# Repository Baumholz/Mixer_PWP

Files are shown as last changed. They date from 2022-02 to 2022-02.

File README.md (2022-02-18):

# PWPHardwareMonkeys

This project consists of two WoT devices. The files for the esp32 can be found in the mixer / dispenser folders.

##  Dispenser

### Requirements

To use the dispenser you need:

- ESP32 (flashed with micropython -> main logic)
- ESP01s (flashed with arduino -> handles button and servo motor logic)
- Switchbot
- Rotary Switch
- Keyboard Switch (Kailh box jade or similar)
- Light Sensor (tsl2591 or similar)
- Cables
- Either Screws, Glue or a Soldering iron to assemble the dispenser
- 3d Printed Parts [STL Files](dispenser/dispenser_stls)

Optionally:
- Ws2812b LED Strip
- Usb-C breakout board for esp01 for easier power delivery

### Structure
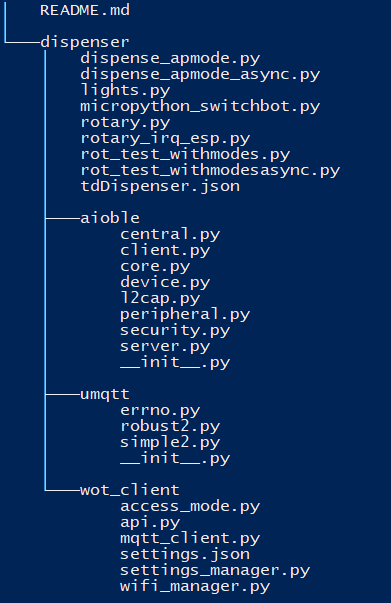
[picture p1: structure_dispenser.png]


### Components / Interfaces
The dispenser has 3 main features

1. [MQTT interface](dispenser/wot_client/api.py) maintained by the modes & communication group 
2. [Switchbot interface](dispenser/micropython_switchbot.py) which can be accessed via API or Bluetooth
3. [Rotary encoder](dispenser/rotary_irq_esp.py) for switching the four security states

### Setup

1. Print and assemble dispenser 
2. Flash esp32 with micropython and wire components to the esp32 (GND and 3.3V/5V can be daisy chained between components)
    1. Connect rotary encoder (clk/s1 = gpio27, dt/s2 = gpio26)
    2. Connect Light sensor to scl and sda (predefined as 5 and 4, but can be changed inside of the tsl2591 python module in line 55)
    3. Optionally: Connect LED Strip to gpio25
3. Copy files on root directory of the esp
4. Configure Wifi credentials in [settings.json](dispenser/wot_client/settings.json)
5. Configure Switchbot bluetooth mac address in [micropython_switchbot.py](dispenser/micropython_switchbot.py) in line 39
6. Run [main.py](dispenser/main.py) on esp
7. Follow instructions of the selected security mode
8. Copy arduino code onto the esp01s and wire components 
    1. connect keyboard switch to gpio2
    2. connect servo motor to gpio0

## Mixer

### Requirements

To use the mixer you need:

- ESP32 (flashed with micropython)
- LEDs
- Rotary Switch
- Mixer
- Cables
- Resistors

### Structure
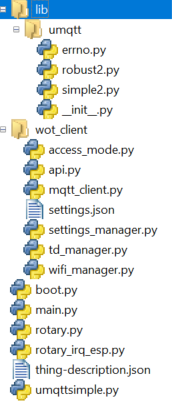
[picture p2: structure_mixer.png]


### Components / Interfaces
The Mixer has 2 main features

1. [MQTT interface](mixer/wot_client/api.py) maintained by the modes & communication group 
2. [Rotary encoder](mixer/rotary_irq_esp.py) for switching the four security states
2. [Mixer interface](mixer/main.py) which can be accessed via API

### Setup

1. Flash esp with micropython
2. Copy files on root directory of the esp
3. Configure Wifi credentials in [settings.json](mixer/wot_client/settings.json)
4. Run [main.py](mixer/main.py) on esp
5. Follow instructions of the selected security mode

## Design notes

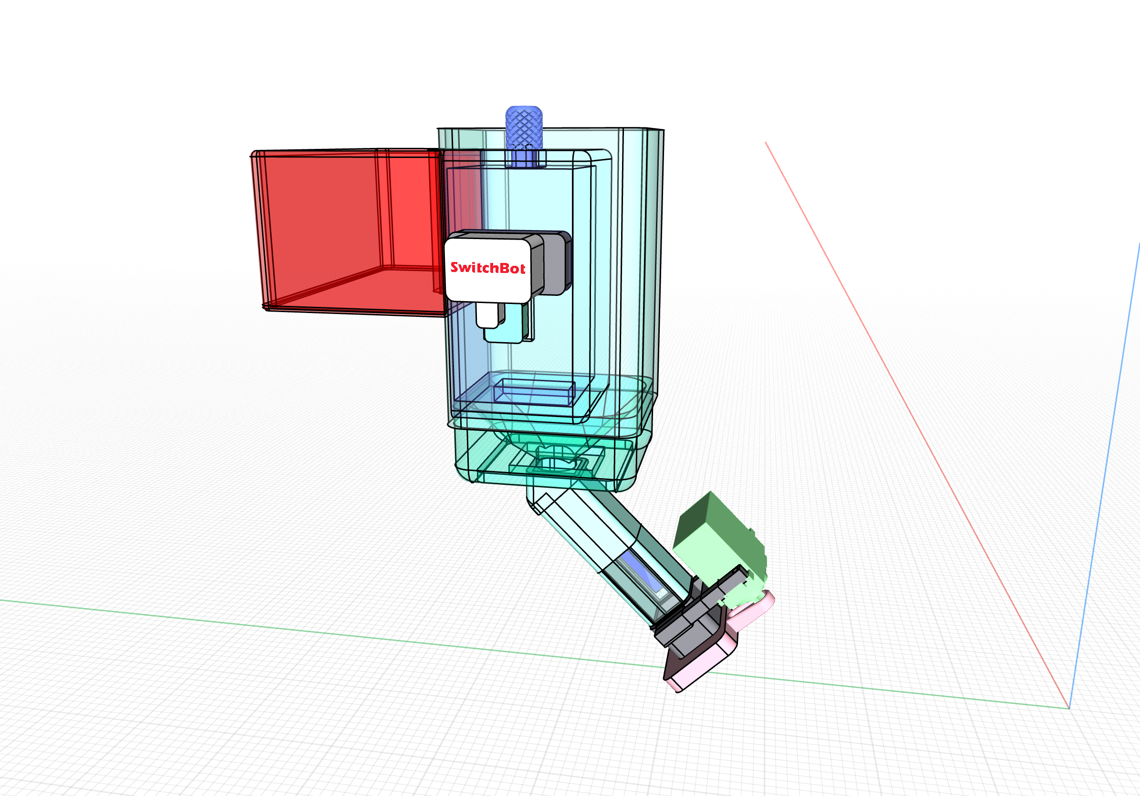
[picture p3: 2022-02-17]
dispenser/dispenser_stls/Dispenser.PNG

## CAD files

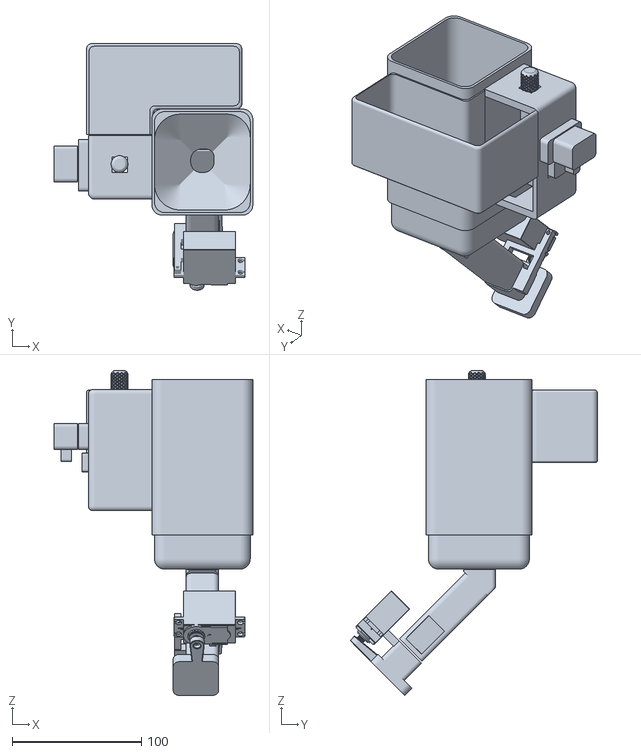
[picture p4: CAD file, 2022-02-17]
dispenser/dispenser_stls/fulldispensermodel.stl
153.5 x 190.6 x 251.1

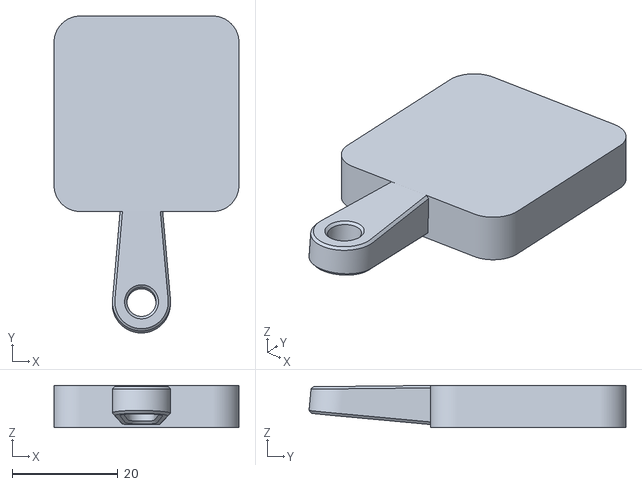
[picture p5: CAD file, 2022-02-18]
dispenser/dispenser_stls/dispenserarm.stl
35.0 x 60.0 x 8.00

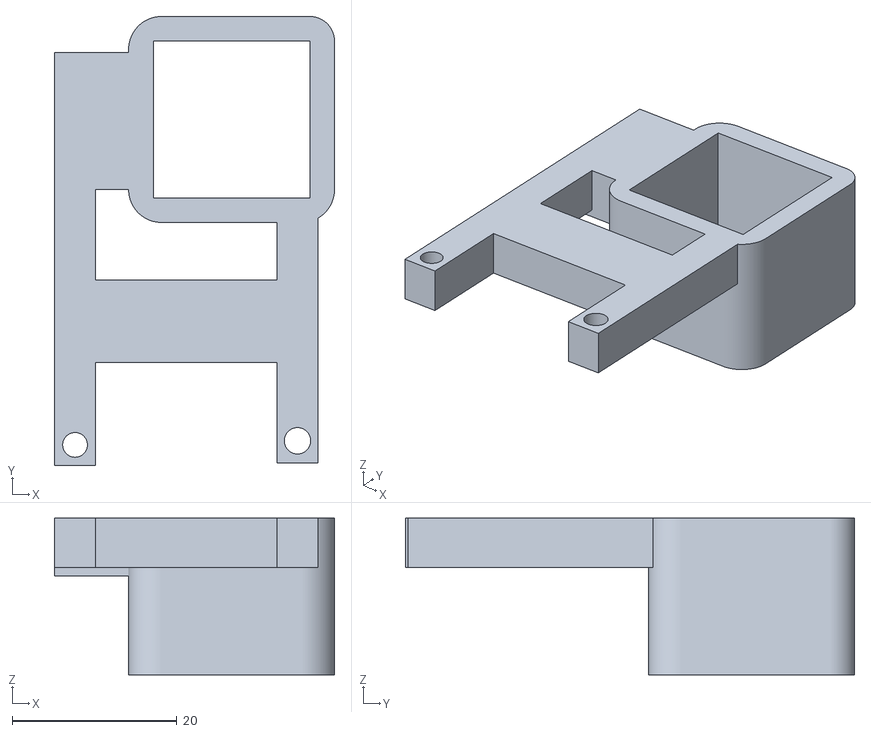
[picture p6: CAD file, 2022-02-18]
dispenser/dispenser_stls/dispenserhole.stl
34.0 x 54.5 x 19.0

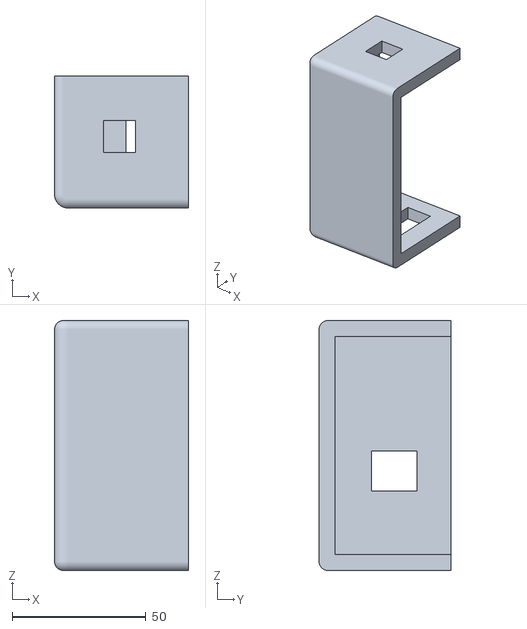
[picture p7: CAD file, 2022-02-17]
dispenser/dispenser_stls/espcontainer.stl
50.1 x 49.4 x 93.5

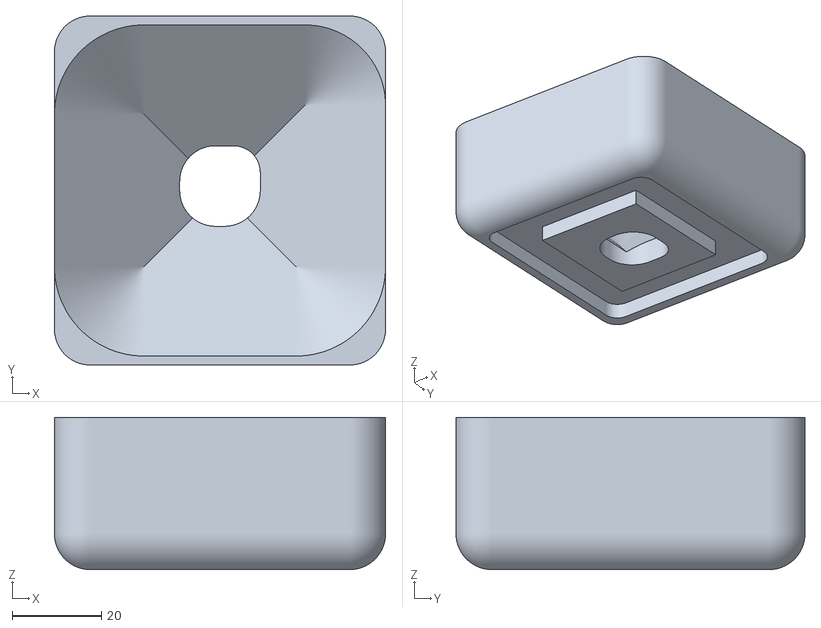
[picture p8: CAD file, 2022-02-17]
dispenser/dispenser_stls/containerp2.stl
74.0 x 78.0 x 34.0

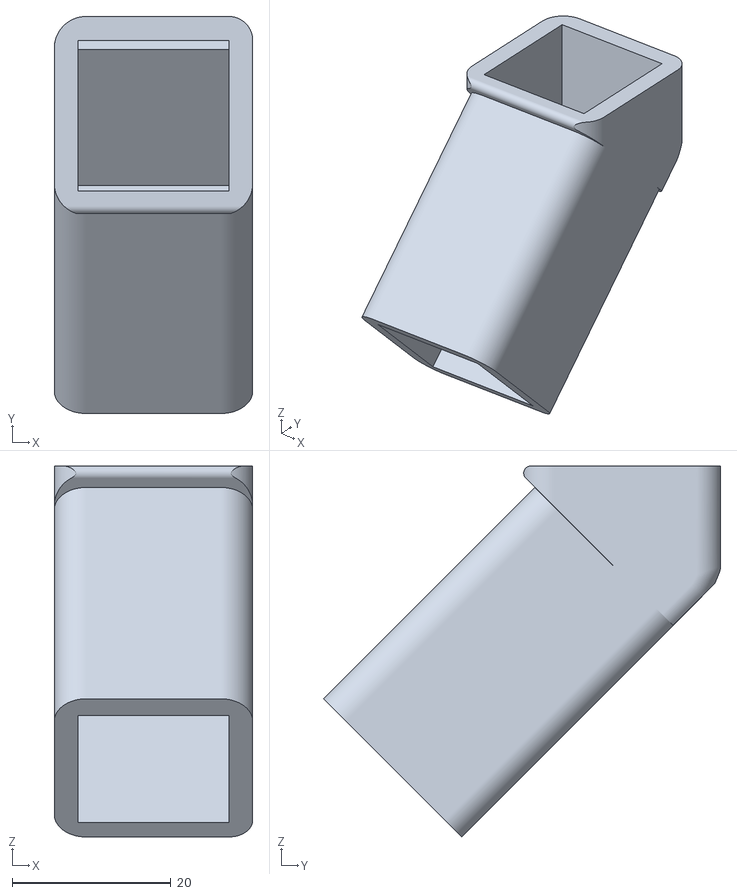
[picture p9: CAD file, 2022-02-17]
dispenser/dispenser_stls/pipep1.stl
25.0 x 50.0 x 46.7

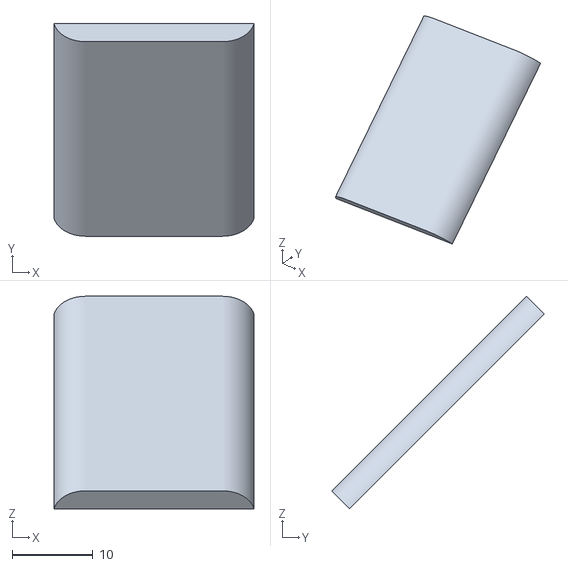
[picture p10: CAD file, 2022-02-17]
dispenser/dispenser_stls/pipetopp1.stl
24.8 x 26.4 x 26.4

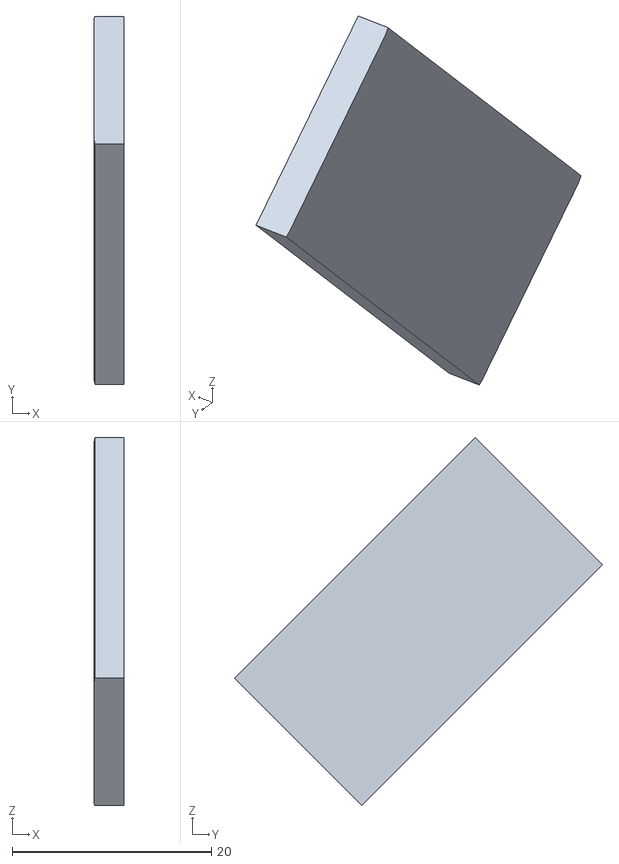
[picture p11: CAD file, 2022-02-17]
dispenser/dispenser_stls/Pipeclearp1.stl
3.00 x 36.9 x 36.9

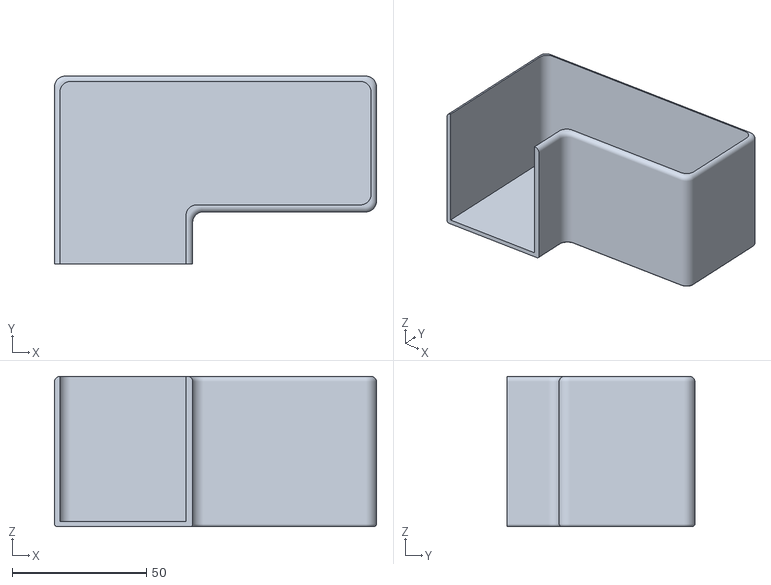
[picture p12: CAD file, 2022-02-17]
dispenser/dispenser_stls/Sidecontainerthin.stl
120.0 x 70.0 x 56.0

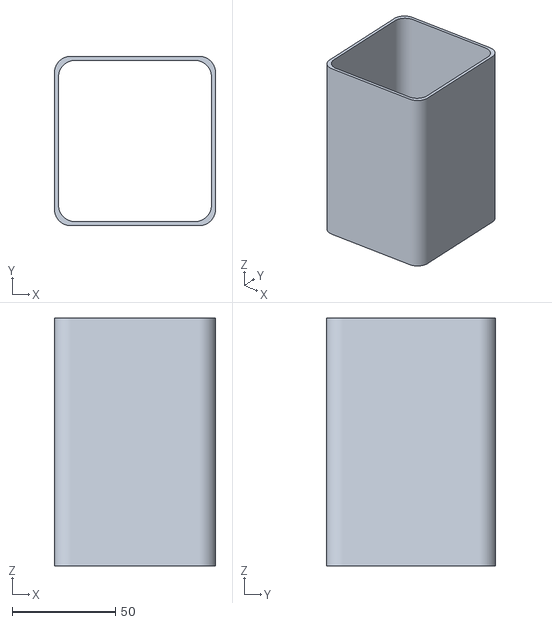
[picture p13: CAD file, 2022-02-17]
dispenser/dispenser_stls/containerp1_thin.stl
78.0 x 82.0 x 120.0

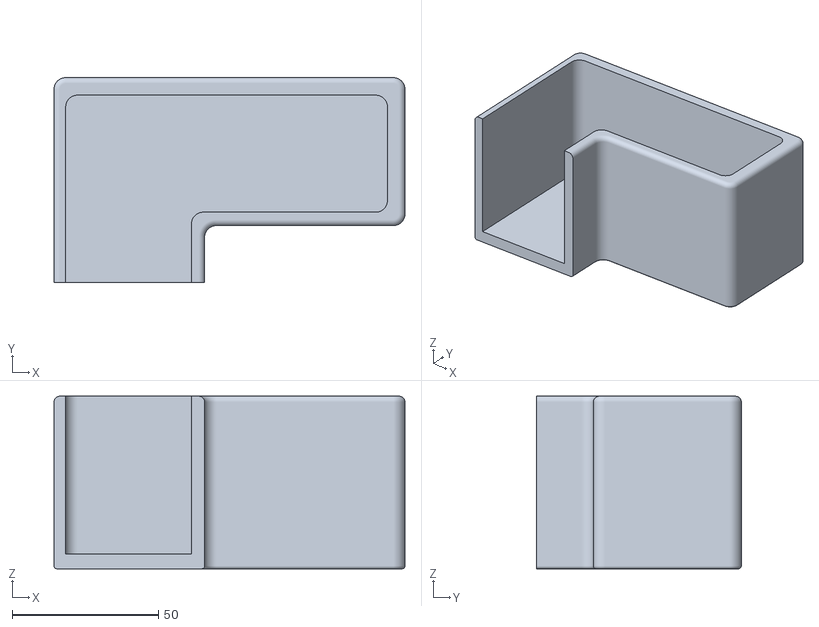
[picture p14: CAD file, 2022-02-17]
dispenser/dispenser_stls/SideContainersmall.stl
120.0 x 70.0 x 59.0

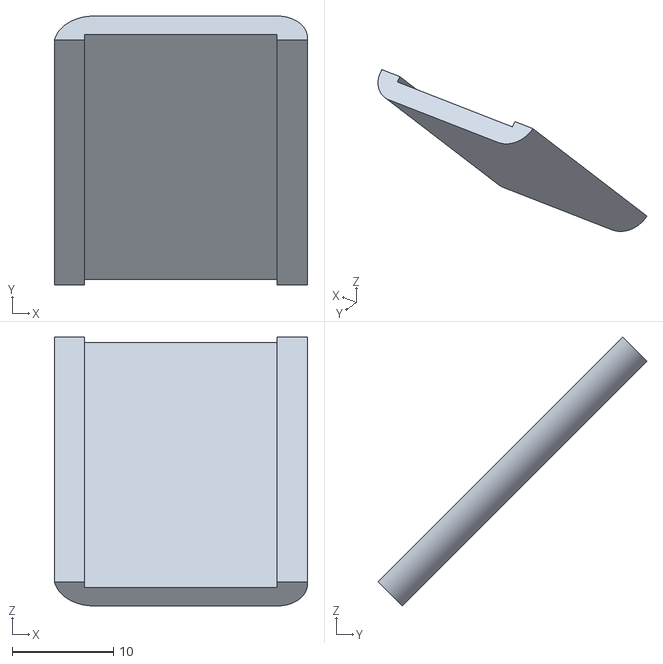
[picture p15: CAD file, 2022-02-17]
dispenser/dispenser_stls/pipebottomp1.stl
25.0 x 26.5 x 26.5

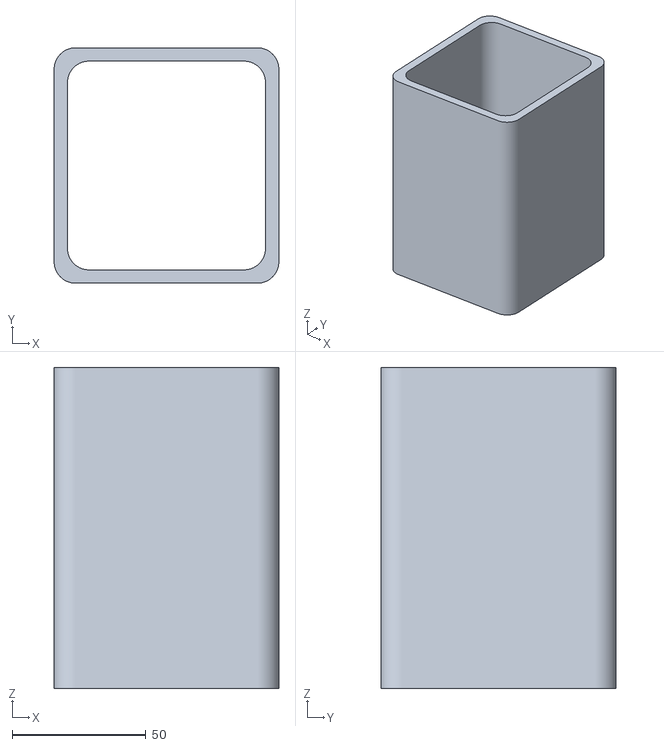
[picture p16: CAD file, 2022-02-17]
dispenser/dispenser_stls/containerp1_thick.stl
84.0 x 88.0 x 120.0

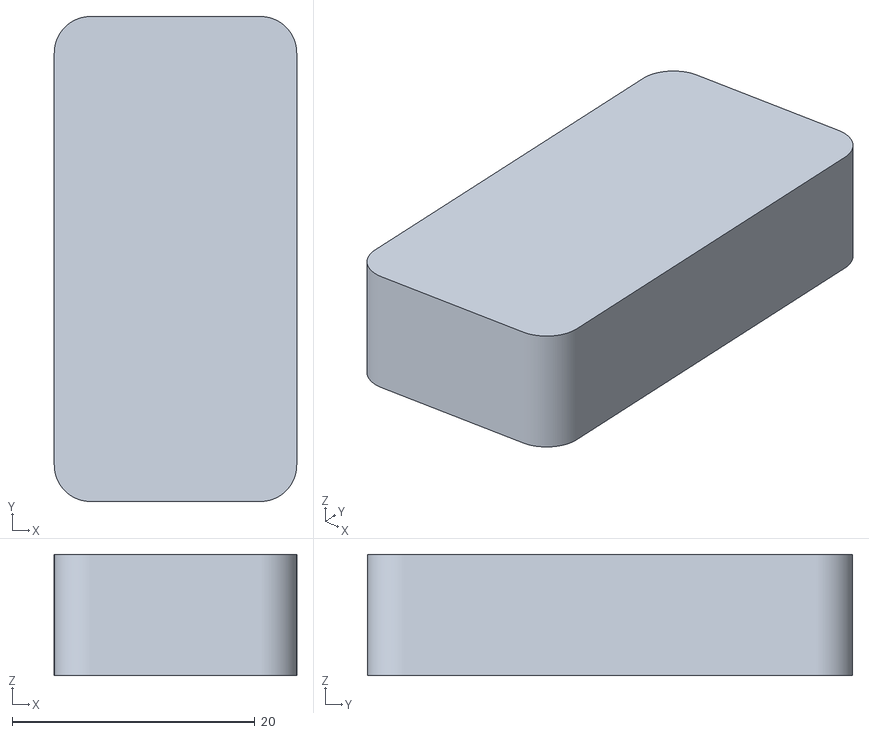
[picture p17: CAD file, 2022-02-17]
dispenser/dispenser_stls/Switchbotstand.stl
20.0 x 40.0 x 10.0

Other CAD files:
dispenser/dispenser_stls/espcontainerlid.stl
dispenser/dispenser_stls/pipeclearp2.stl
dispenser/dispenser_stls/SideContainer.stl

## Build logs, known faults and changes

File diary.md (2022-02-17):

# Diary: Hardware Group Winter Term 21/22

**Step 1: Ideation Phase** _(about 1 week)_

- Get to know each other
- Finding possible problems and use cases for WoT
- Brainstorming project ideas
- Documenting the ideas
- Presenting the ideas
- Deciding on a product/solution (dispenser/mixer)
- Separating in subteams and communicating with other groups
- Ordering hardware

**Step 2: Implementation Phase** _(about 2 weeks)_

Subteam Mixer:

- Testing the different sensors, rotation switch and socket adapter
- Writing the first code
- Dropping the vibration sensor and socket adapter
- Deciding on using switching contact for On/Off
- Ordering new rotation switch
- Testing the new rotation switch
- Soldering, gluing and building the mixer hardware
- Creating Thing Description for device
- Implementing switch and modes code
- Making UI for the AP mode
- Bug fixing (Switching between AP and other modes)

Subteam Dispenser:

- Setting up the esp and writing small code snippets for parts of the dispenser logic
  - MQTT in micropython
  - Switchbot API in micropython
  - Servo Motor in micropython → later implemented in arduino on a separate esp01
- Creating Thing Description for device
- 4-step switch setup → proved to be unreliable, replaced with rotary encoder
- Fixing mode switch for new rotary using asynchronous tasks
- Getting esp to work with low power bluetooth devices
- Re-writing switchbot python library in micropython
- Designing dispenser in cad software
- 3d printing and assembling dispenser
- Soldering/wiring esp with sensors and other hardware
- Dealing with broken hardware scheduling team coordination
- Thinking about possible solutions to provide the bluetooth api in offline mode
- Bug fixing (Switching between AP and other modes in async)
- Huge communication between all groups

**Step 3: Final Phase** _(about 1 week)_

- Tested Mixer and Dispenser hardware on the different security level
- Testing the Modes/Communication API
- Testing and combining with the other groups
- Making of the product video (planing, meeting, shooting and editing)
- Making of the presentation

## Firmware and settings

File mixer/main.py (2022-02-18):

from time import sleep_ms, sleep
import math
from rotary_irq_esp import RotaryIRQ
from machine import Pin
import json
from wot_client import api
import uasyncio
import ure
import _thread
import utime
import time

def handle_interrupt(pin):
    global val_power_old
    value = pin.value()
    print(value,val_power_old)
    #if val_power_old == value:
    #    return
    if value:
        api.publish_property_value("status", True)
        print("INTERRUPT_TRUE")
    else:
        api.publish_property_value("status", False)
        print("INTERRUPT_FALSE")
    val_power_old = value

OnOff = Pin(26, Pin.IN, Pin.PULL_UP)
OnOff.irq(trigger=Pin.IRQ_RISING | Pin.IRQ_FALLING, handler=handle_interrupt)

LED_MIX = Pin(25, Pin.OUT)
api.init()
length = 0

LED_ROTTARY_ONE = Pin(33, Pin.OUT)
LED_ROTTARY_TWO = Pin(32, Pin.OUT)
LED_ROTTARY_THREE = Pin(5, Pin.OUT)
LED_ROTTARY_FOUR = Pin(17, Pin.OUT)

print(api.get_device_id())        

def get_rotaryvalue(v):
    return math.floor(v/5)

r = RotaryIRQ(pin_num_clk=16, 
              pin_num_dt=4, 
              min_val=0, 
              max_val=19, 
              reverse=False, 
              range_mode=RotaryIRQ.RANGE_WRAP)
              
val_rot_old = get_rotaryvalue(r.value())
val_power_old = 0

#AP-MODE
def web_page(length):
  
  html = """<html><head><title>Mixer AP Mode</title> <meta name="viewport" content="width=device-width, initial-scale=1">
  <link rel="icon" href="data:,"> <style>html{font-family: Helvetica; display:inline-block; margin: 0px auto; text-align: center;}
  h1{color: #0F3376; padding: 2vh;}p{font-size: 1.5rem;}
  .button{display: inline-block; background-color: #e7bd3b; border: none; 
  border-radius: 4px; color: white; padding: 16px 40px; text-decoration: none; font-size: 30px; margin: 2px; cursor: pointer;}
  }</style></head><body> <h1>Mixer AP Mode</h1> 
  <h2>Mixer Configuration</h2>
  <form enctype="multipart/form-data" method="get">
    <label>Mixing time in secounds</label><br/>
    <input type="number" id="length" name="length" step="any" value='""" + str(length) + """'><br><br>
    <input class="button" type="submit" value="Send">
  </form>
  </body></html>"""

  return html

s = socket.socket(socket.AF_INET, socket.SOCK_STREAM)
#bind socket with portnumber and IP Address ('' for localhost)
s.bind(('', 80))
s.listen(5)
s.setblocking(False)

def mix(duration):
    LED_MIX.on()
    print("start mix")
    while not OnOff.value():
        time.sleep(0.5)
    api.publish_property_value("status", True)
    timer(duration)
    #_thread.start_new_thread(timer(duration),())
    
    
def timer(duration):
    unexpected = False
    totalduration = duration
    while duration > 0:
        current_time = utime.time()
        while OnOff.value():
            unexpected = True
            tmp = utime.time()
            delta = tmp - current_time
            current_time = tmp
            duration -= delta
            print("U_TIME: " + str(utime.time()))
            print("TIME: " + str(duration))
            time.sleep(0.1)
            if duration <= 0:
                LED_MIX.off()
        if totalduration != duration and unexpected and duration > 0:
            unexpected = False
            print("unexpectedturnoff")
            api.publish_event("unexpectedturnoff", True)
        time.sleep(0.3)
        

def ap(callback):
    while True:
        try:
            print("bin in ap")
            conn, addr = s.accept()
            print('Got a connection from %s' % str(addr))
            request = conn.recv(1024)
            request = str(request)
            print('Content = %s' % request)
            
            length = ure.search(r"/?length=(.*?) HTTP", request)
            print("legnth:",length)
            if length != None:
                length = length.group(1)
                if length:
                    mix(float(length))
            print(length)
            
            response = web_page(length)
            conn.send('HTTP/1.1 200 OK\n')
            conn.send('Content-Type: text/html\n')
            conn.send('Connection: close\n\n')
            conn.sendall(response)
            conn.close()
        except OSError:
            val = callback()
            if val != 1 or val != 2:
                return    
            time.sleep(0.5)
  
def onoff(val_power_new):
    global val_power_old
    print(val_power_old)
    if val_power_old != val_power_new:
        val_power_old = val_power_new
        if val_power_new == 0:
            api.publish_property_value("status", True)
        else:
            api.publish_property_value("status", False)


def example_on_action_handler(topic, msg):
    print('I am the example on_action_handler!', topic, msg)
    mix(float(msg))
    
    
api.set_on_action_handler(example_on_action_handler)

def turn_leds_on(count):
    if count == 0:
        LED_ROTTARY_ONE.on()
        LED_ROTTARY_TWO.off()
        LED_ROTTARY_THREE.off()
        LED_ROTTARY_FOUR.off()
    elif count == 1:
        LED_ROTTARY_ONE.on()
        LED_ROTTARY_TWO.on()
        LED_ROTTARY_THREE.off()
        LED_ROTTARY_FOUR.off()
    elif count == 2:
        LED_ROTTARY_ONE.on()
        LED_ROTTARY_TWO.on()
        LED_ROTTARY_THREE.on()
        LED_ROTTARY_FOUR.off()
    elif count == 3:
        LED_ROTTARY_ONE.on()
        LED_ROTTARY_TWO.on()
        LED_ROTTARY_THREE.on()
        LED_ROTTARY_FOUR.on()

def rotated():
    global val_rot_old, r
    val_rot_new = get_rotaryvalue(r.value())
    print("VAL_OLD:",val_rot_old)
    print("VAL_NEW:",val_rot_new)
    if val_rot_old != val_rot_new:
        turn_leds_on(val_rot_new)
        val_rot_old = val_rot_new
        print('result =', val_rot_new)
        api.set_access_mode(val_rot_new)
        api.publish_property_value("access_mode",val_rot_new)
    return val_rot_new

LED_ROTTARY_ONE.on()
while True:
    r.add_listener(rotated)
    val_rot_new = get_rotaryvalue(r.value())
    print(val_rot_new)           
    #TODO: add the code to switch the mode and run the different functions        
    if val_rot_new == 1 or val_rot_new == 2:
        ap(rotated)                    
    sleep_ms(1000)

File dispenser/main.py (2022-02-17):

import time
import math
from rotary_irq_esp import RotaryIRQ
import wot_client.api as apiX
import sys
from dispense_apmode_async import ap_mode
from micropython_switchbot import run_on_api
from light import init_lights
import uasyncio as asyncio

sys.path.reverse()
apiX.init()
init_lights()

class Action:
    def __init__(self, mode):
        self.set_mode(mode)
        
    def set_mode(self, new_mode):
        self.mode = new_mode
        print("mode: ", self.mode)
        apiX.set_access_mode(new_mode) 
        
default_mode = 0
a = Action(default_mode)

def init():
    r = RotaryIRQ(pin_num_clk=27, 
                  pin_num_dt=26, 
                  min_val=0, 
                  max_val=19, 
                  reverse=False, 
                  range_mode=RotaryIRQ.RANGE_WRAP)
                  
    val_old = math.floor(r.value()/5)
    return r, val_old


def example_on_action_handler(topic, msg):
    run_on_api(int(msg), apiX.publish_event)

apiX.set_on_action_handler(example_on_action_handler)

r, val_old = init()

val_old = r.value()
def rotated():
    """check if rotary value changed"""
    global val_old
    val_new = math.floor(r.value()/5) 
    if val_old != val_new:
        val_old = val_new
        print('result =', val_new)
        a.set_mode(val_new)
        apiX.publish_event("access_mode", str(val_new))
        return True
    return False

async def check_modes(task):
    """Kill ap mode if value changed"""
    print(a.mode)
    if rotated() and task:
        task.cancel()  
    await asyncio.sleep_ms(1_000)

async def main():
    """
    Start tasks in parallel
    """
    task = None
    if a.mode == 1 or a.mode == 2:
        task = asyncio.create_task(ap_mode(apiX.publish_event))
    asyncio.create_task(check_modes(task))
    await asyncio.sleep_ms(10_000)
    
def rotary_send():
    while True:
        print("ready to publish event")
        r.add_listener(rotated) 
        asyncio.run(main())
        time.sleep_ms(5000) 


rotary_send()

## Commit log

2022-02-01 added led lights to the dispenser
2022-02-02 fixed async and normal mode
    [dispense_apmode.py, dispense_apmode_async.py, rot_test_withmodes.py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]
2022-02-17 added dispenser 3d print files, esp01 code
    [Pipeclearp1.stl, SideContainer.stl, SideContainersmall.stl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]
2022-02-17 added notes in readme, full dispenser model
    [fulldispensermodel.stl]
2022-02-18 added more stl files, added hardware parts to readme
    [dispenserarm.stl, dispenserhole.stl]
